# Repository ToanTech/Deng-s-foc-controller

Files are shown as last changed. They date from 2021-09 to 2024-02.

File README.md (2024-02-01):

# 灯哥开源FOC双路无刷电机控制器

      灯哥开源 FOC 控制器是一个由灯哥开源的，基于 [GPL-3.0](https://github.com/ToanTech/Deng-s-foc-controller/blob/master/LICENSE) 开源协议和ESP32主控的低成本无刷电机双路FOC驱动控制板。双路总功率 240W，单路最大功率 120W，支持绝大部分的云台电机FOC 位置、速度、力矩开闭环控制。编码器方面支持常见IIC和ABI、PWM制式。**加入在线电流检测模块，实现真正完整的FOC控制**。总的来说， 灯哥开源 FOC 控制器是一个好用又便宜的双路无刷FOC驱动器，点击查看 [效果视频](https://www.bilibili.com/video/BV1Hz4y127FL/)。

     灯哥开源无刷FOC目前的发展受到灯哥开源团队的深度支持，目前已经针对这块控制板开发出了[灯哥开源无刷四足机器人](https://github.com/ToanTech/py-apple-bldc-quadruped-robot)，DIY视频和效果见：[B站](https://www.bilibili.com/video/BV1kV411i76z/)，后续还有无刷平衡车，倒立摆等等运行示例推出，敬请关注。

* **目前该主控板已经上架淘宝，是焊接好调试好的成品，出售即包括 ESP32** ；有需要大家可以猛击[淘宝链接（进店后在 所有宝贝 处可找到）](https://shop564514875.taobao.com/)

* 开源工作不易，希望大家多点 Star ,视频多一键三联！！！

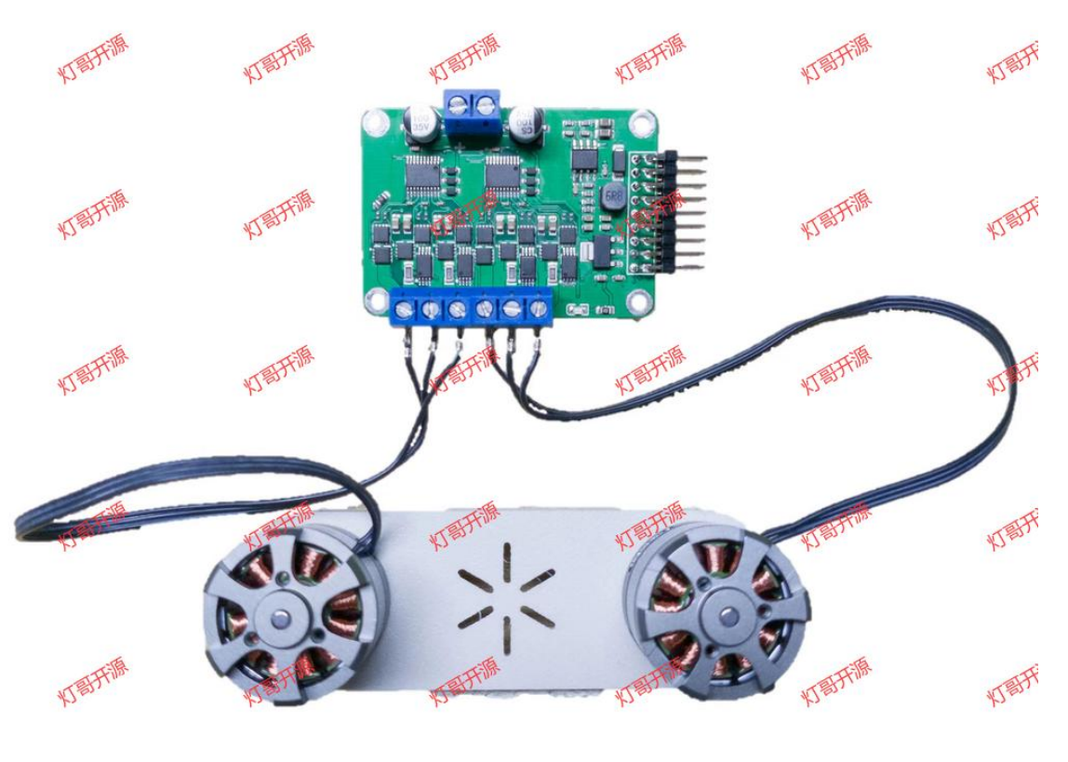
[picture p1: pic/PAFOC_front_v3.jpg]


## 1 软件特性（支持 SimpleFOC库 2.2.2--最新库）

  作为国内最早引入 SimpleFOC 的团队，我们一直在致力深度改进 SimpleFOC硬件使其本土化，让大家能够以低廉的价格玩动无刷FOC算法。SimpleFOC是一个支持强大的开源库，可以实现无刷电机开闭环力矩、速度、位置控制，具体特性如下：

- **基于 Arduino**：运行在 ESP32 Arduino 上

- **开源**: 所有代码和配置文档都可以在：[SimpleFOC文档页](https://docs.simplefoc.com/) 找到

- **轻量化**：相比 Odrive 等驱动器，更加轻量化的软件结构可以帮你高速完成算法学习及配置

- **控制模式丰富**：开/闭环 速度、位置；以及开环的基于力矩控制；两种FOC内核算法

- **图形化配置软件**:最新的 DengFOC 对应支持使用 **SimpleFOC Studio** 进行电机参数配置，如下图所示，配置方法请见 文档PDF

  

## 2 硬件特性

| 说明 | 参数 |
| --- | --- |
| 尺寸 | 56*39 mm |
| 输入电压类型 | 直流DC |
| 输入电压 | 12-24V |
| 最大功率 | 单路120W 双路共240W |
| 支持电机数 | 2 |
| 主控 | 底面搭载ESP32开发板 lolin32 lite |
| 编码器支持 | IIC方式、ABI方式、PWM方式编码器(AS5600、AS5047、AS5048等)、SPI方式、HALL编码器 |
| 拓展接口 | 串口（可以通过串口对FOC板子进行控制） |
| 电流检测参考电压 | 3.3V |
| 电流检测最大电流 | 3.3A |

## 3 重要链接

本 FOC 库与 DengFOC 硬件联合组成一整套完整可用的 FOC 电机驱动方案，资料链接：

1 [灯哥开源 淘宝店--一站配齐DengFOC板](https://shop564514875.taobao.com/) 您的支持就是我们持续做开源内容和课程的动力，项目收益将用于后续开发DengFOC和做课程~

2 [DengFOC库 Github](https://github.com/ToanTech/DengFOC_Lib)

3 [DengFOC官网](http://dengfoc.com/#/) 包含课程文字版讲义，DengFOC使用文档，库使用方法等。

## 4 社区

本FOC板子社区唯三Q群，欢迎加入：**开源FOC无刷驱动交流群 灯哥开源 群号 778255240（1群） 735755513（2群）471832283（3群） 834835665（4群）247431752(5群)**

任何使用问题和 DIY 问题 都会在这里做直接的讨论解答

## 5 项目文件说明

* Dengs FOC V3.0 DIY资料：BOM、原理图、PCB、Gerber
* Dengs FOC V3.0 测试例程：21个灯哥开源FOC开环、闭环、应用方面的测试视频
* 灯哥开源 FOC 使用文档 PDF：**配置的详细方式和使用教程**

## 6 DengFOC配套应用实践项目

利用DengFOC做的有趣的无刷电机实践项目：

[1 动量轮倒立摆项目，低成本化和小型化后应用在DengFOC上](https://github.com/ToanTech/Inverted_Pendulum_DengFOC)

[2 自平衡 DengFOC莱洛三角形](https://github.com/ToanTech/Lailuo_DengFOC)

[3 自平衡 DengFOC无刷平衡车](https://github.com/ToanTech/Balance_Bot_DengFOC)

[4 基于DengFOC的无刷四足并联腿机器狗](https://github.com/ToanTech/py-apple-bldc-quadruped-robot)

## 7 免费手把手教写FOC算法原理课

为了方便大家更进一步的理解FOC的算法和原理，我做了手把手教些FOC算法原理课，通过这些原理课你能够快速的从原理角度理解FOC知识并尝试写出自己的FOC基本功能库，视频链接：

1 [【手把手教写FOC算法】1_起源，无刷电机概念与控制原理](https://www.bilibili.com/video/BV1dy4y1X7yx)

2 [【手把手教写FOC算法】2_克拉克变换，建立简化电机数学模型](https://www.bilibili.com/video/BV1x84y1V76u/)

3 [【手把手教写FOC算法】3_等幅值变换与克拉克逆变换](https://www.bilibili.com/video/BV13s4y1Z7Tg/)

4 [【手把手教写FOC算法】4_帕克变换](https://www.bilibili.com/video/BV1t24y1u7do/)

5a [【手把手教写FOC算法】5a_撰写开环速度代码的前置知识](https://www.bilibili.com/video/BV1Pc411s7mP/)

5b [【手把手教写FOC算法】5b_开环速度代码编程+硬件调试教学](https://www.bilibili.com/video/BV16X4y167XZ/)

6a [【手把手教写FOC算法】6a_撰写闭环位置代码的前置知识](https://www.bilibili.com/video/BV1Rm4y1871K/)

6b [【手把手教写FOC算法】6b_闭环位置代码编程+硬件调试教学](https://www.bilibili.com/video/BV1yh4y1J7Xx/)

7a1 [【手把手教写FOC算法】7a1_写闭环速度代码的前置知识](https://www.bilibili.com/video/BV18m4y1v75j/?spm_id_from=333.788&vd_source=365d5478018f3e4c39b71b3dd6a7dd0a)

7a2[【手把手教写FOC算法】7a2_速度低通滤波器](https://www.bilibili.com/video/BV16h4y1X7gZ/?spm_id_from=333.999.0.0)

7a3 [【手把手教写FOC算法】7a3_速度PI控制器](https://www.bilibili.com/video/BV17s4y1y767/?spm_id_from=333.999.0.0)

7b [【手把手教写FOC算法】7b_闭环速度代码编程+硬件调试教学](https://www.bilibili.com/video/BV1tu4y1o7WU/?spm_id_from=333.999.0.0)

8a [【手把手教写FOC算法】8a_撰写电流环代码的前置知识](https://www.bilibili.com/video/BV1z14y1v7yS/?spm_id_from=333.999.0.0)

8b [【手把手教写FOC算法】8b_精确电流力矩环代码编程+硬件调试教学](https://www.bilibili.com/video/BV1Sh4y1Q7ue/?spm_id_from=333.999.0.0)

9a[【手把手教写FOC算法】9a_用电流环改进速度和位置闭环-前置知识](https://www.bilibili.com/video/BV1Zy4y1A7pL/)

9b[【手把手教写FOC算法】9b_电流环改进速度和位置闭环代码编程+硬件调试教学](https://www.bilibili.com/video/BV1dy4y1N798/)

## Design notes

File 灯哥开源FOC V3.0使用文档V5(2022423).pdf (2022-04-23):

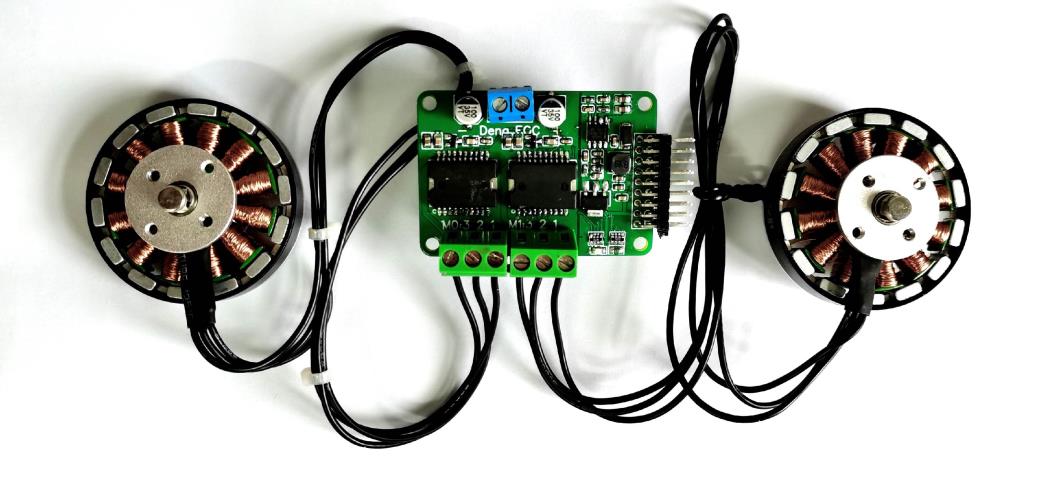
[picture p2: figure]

# 灯哥开源 FOC V3.0

使用说明文档 V5

2022.4.23 更新

1

目录

6 从 0 开始焊接电路板（针对自行 DIY 此 FOC 驱动的爱好者） .....15

2

## 1 概述

灯哥开源 FOC 控制器是一个由灯哥开源的，基于 GPL-3.0 开源

协议和 ESP32 主控的低成本无刷电机双路 FOC 驱动控制板。双路总功

率 240W，单路最大功率 120W，支持绝大部分的云台电机 FOC 位

置、速度、力矩开闭环控制。编码器方面支持常见 IIC 和 ABI、PWM、

Hall、SPI 制式。加入在线电流检测模块，实现真正完整的 FOC 控制。

总的来说，灯哥开源 FOC 控制器是一个好用又便宜的双路无刷 FOC

驱动器。

在 V3 版本中，加入电流检测放大器 INA240A2，通过采样与电机

相串联的采样电阻电压获得 A、B 相电流，应用于电流环控制，构建

出真正，完整的 FOC 算法。

灯哥开源无刷 FOC 目前的发展受到灯哥开源团队的深度支持，目

前已经针对这块控制板开发出了灯哥开源无刷四足机器人，后面更会

开发出更多好玩的应用，例如平衡车，倒立摆等等，敬请关注。

## 2 性能简介

### 2.1 总体性能

目前灯哥开源双路 FOC 的具体技术性能指标如下：

单路最大功率 | 120W（双路 240W）
支持电压 | 12V-24V
支持的无刷电机类型 | 云台电机（相电阻>10 欧）

3

支持同时驱动的电机数量 | 2
支持的编码器通讯方式 | IIC ABI PWM Hall SPI
支持的外部控制方式 | 串口控制 WIFI 无线控制
支持的电流检测方式 | 在线电流检测
电流检测电压 | 3.3V
电流检测最大电流 | 3.3A

### 2.2 驱动板支持的电机选型

灯哥开源 FOC 目前支持常见的云台电机，具体选型指标主要有两

点：

◼ 电机相电阻>10Ω

◼ 最大运行电流在 5A 左右

这两个选型指标基本上能够覆盖大部分的云台电机，所以基本上只

要选择云台电机就可以正常的使用这个板子，若按照 KV 数进行选择，

建议选择 200KV 以下的电机。

若对云台电机的选型有疑问，或者需要验证选型是否正确，可以加

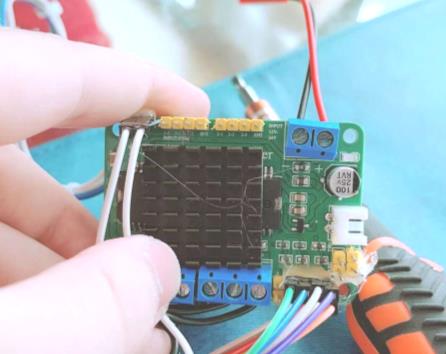
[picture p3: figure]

4

入 Q 群：778255240 详细询问，热心的群友将会给你解答，灯哥我看

到了也会及时回复。

## 3 基础配置及运行

### 3.1 线路连接及其实例

灯哥开源 FOC V3 的线路连接与 V2 相同，极其简单，只需要连上电

源线和电机线，就已经可以使得板子正常的运行开环控制；在此基础

上，再连接上编码器，就可以使 FOC 控制板实现闭环控制。

注意：若需要长时间调试或使用，你得加上散热片，良好的散热能

够使得 FOC 的性能得到充分发挥！实验证明，大部分运行过程中突

然的卡顿。震动都来自于 FOC 散热不良！！在高电压电流的情况下，

不良的 FOC 散热有可能导致驱动芯片烧毁。在默认情形下，灯哥官

方建议一般都必须加上散热片使用！

推荐的散热片尺寸为 25x25 铝制散热片，安装效果如下图所示：

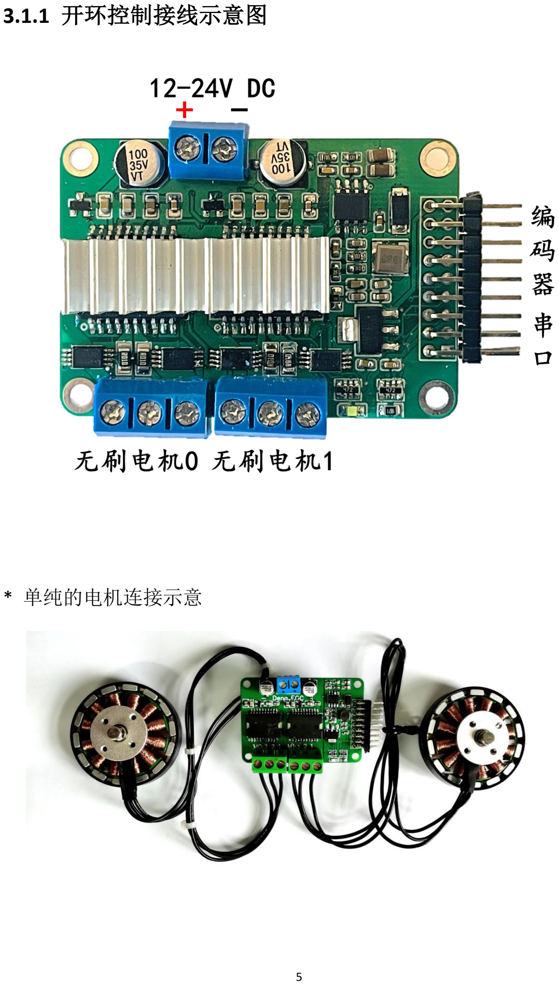
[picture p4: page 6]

5

### 3.1.1 开环控制接线示意图

* 单纯的电机连接示意

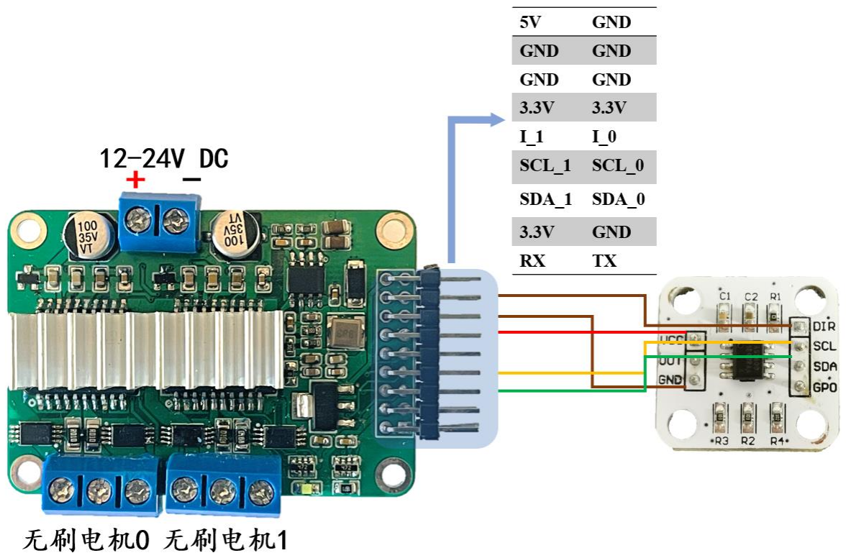
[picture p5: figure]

6

### 3.1.2 闭环控制接线图（基于 AS5600）

由于图幅限制，只展示一个电机配合一个编码器的接线，两个电

机的接线亦同理，具体例程请参照例程文件夹。

### 3.1.3 闭环控制接线图（基于 AS5047P）

由于图幅限制，只展示一个电机配合一个编码器的接线，两个电

机的接线亦同理，具体例程请参照例程文件夹。

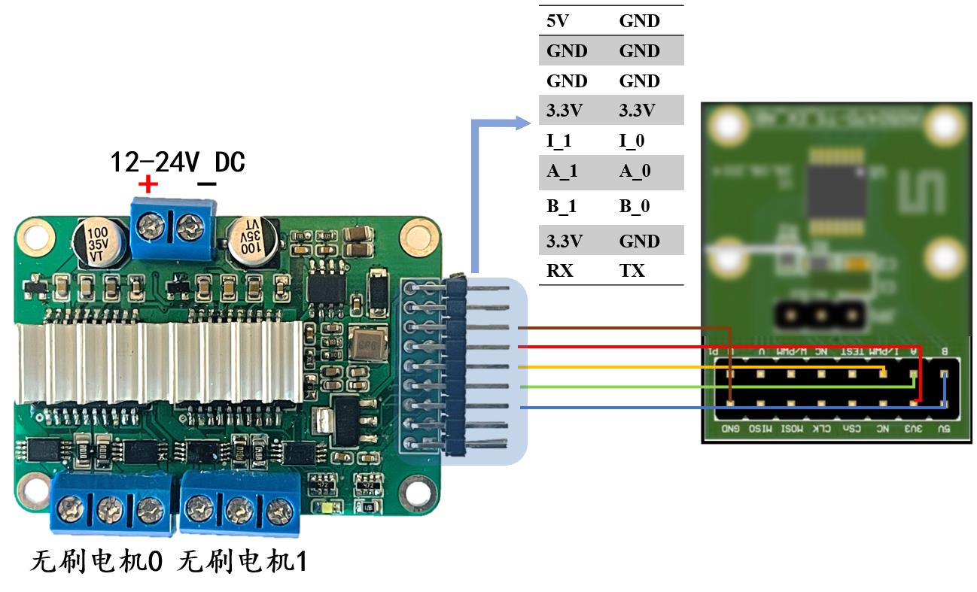
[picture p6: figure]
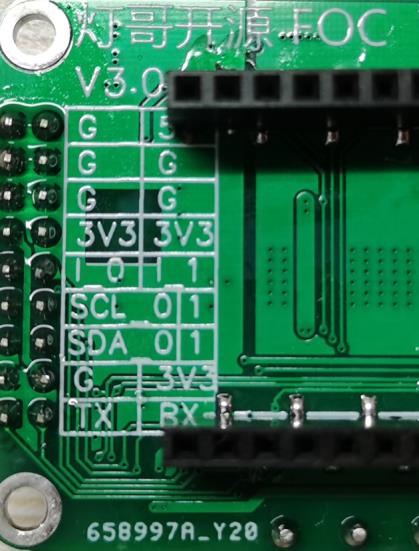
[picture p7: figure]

7

* 底面均有引脚示意

在完成了对应的接线，通电确定驱动板灯亮之后，就可以进入我

们的下一步：编程环境配置

### 3.2 编程环境配置

灯哥开源 FOC 由于使用基于 SimpleFOC 的库运行，因此软件环境配

8

置也与 SimpleFOC 库相同，默认都采用 Arduino IDE 作为主程序编程

/编译软件。

最新测试过能够完美支持灯哥开源 FOC 的软件版本为：

✓ Arduino IDE 1.8.19

✓ SimpleFOC Library 2.2.1

✓ ESP32 Arduino Libiary 2.0.2

针对上面的软件版本，我已经做好整合包，大家直接下载解压就可

以使用，避免繁杂的环境配置，下载地址：

⚫ 链接：

https://pan.baidu.com/s/13VfSVINak0wqCzG9hRQUYA?pwd=wumh

⚫ 提取码：wumh

当完成下载后，解压下载的文件，点击文件中的 arduino.exe 即可

打开软件，开始编译例程，愉快的玩耍。

注意：解压前建议清除原有 Arduino 的环境；解压路径不要有中文路

径。

完成安装后，即可编译本项目提供的例程。并且进行程序的编写。

在下幅图中，点击左上角的“√”进行程序的编译，当电脑连接了

FOC 控制板后，点击左上角的“→”进行程序上传，接下来就可以畅

快的玩耍了。

注意，开发板必须选择：ESP32 DEV Module,具体选择方式如下,

必须如图上设置好之后才能编译并且使用：

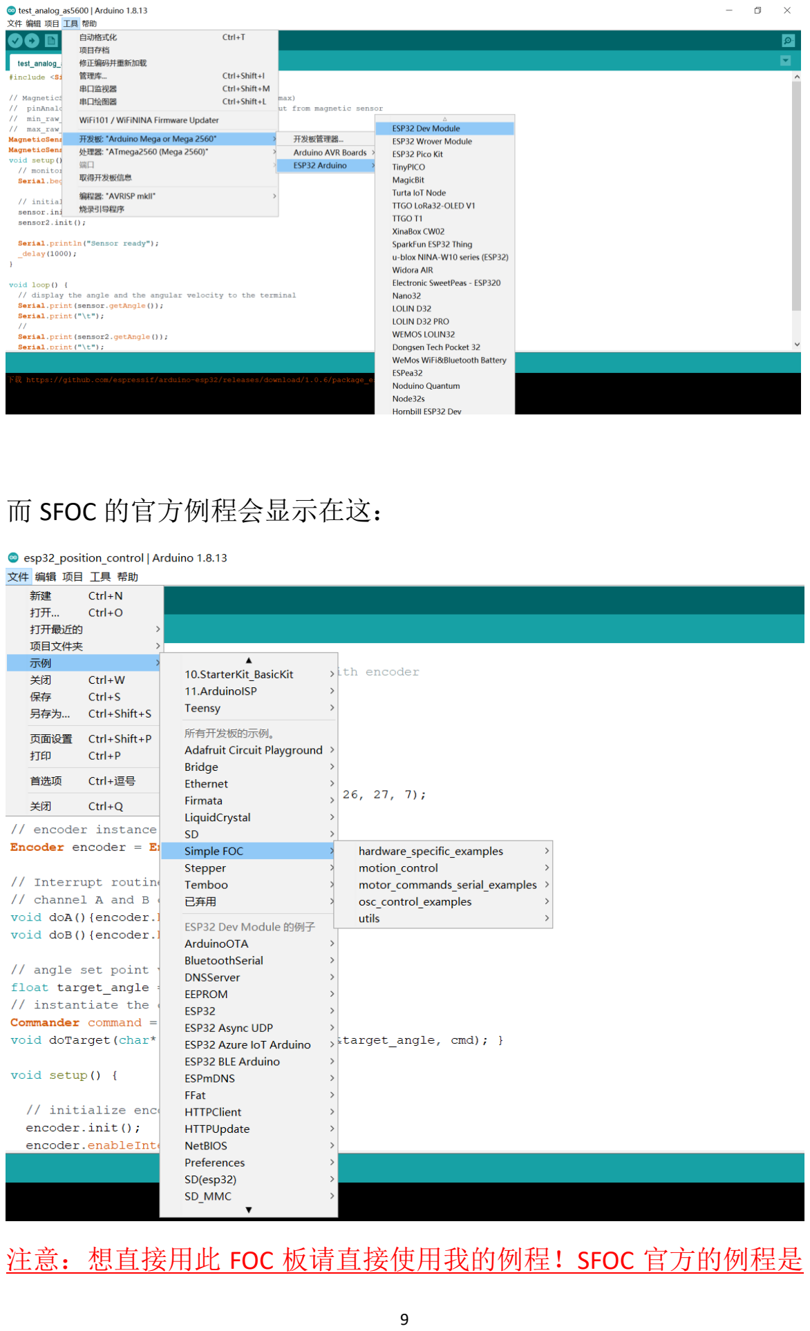
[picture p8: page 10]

9

而 SFOC 的官方例程会显示在这：

注意：想直接用此 FOC 板请直接使用我的例程！SFOC 官方的例程是

10

针对官方板子的，引脚不一样！不修改不能直接用在此板子上！而我

给大家的例程都是已经改好调试过的！！

## 4 Simple FOC Studio 在线调参工具

4.1 简介

SimpleFOC Studio 是一个可用于图形化配置 SimpleFOC，并且对电

机进行在线 PID 调参的工具，非常好用，主要特性包括：

1. 电机参数的实时调整和配置
2. 电机状态的实时绘图和监控
3. 可以根据配置好的参数自动生成代码，以植入到自己的程序中
4. 基于 PyQT5 安装配置简单，兼容性好。

软件的操作界面如下图所示，在本章中，将会详细讲述它的配置方式。

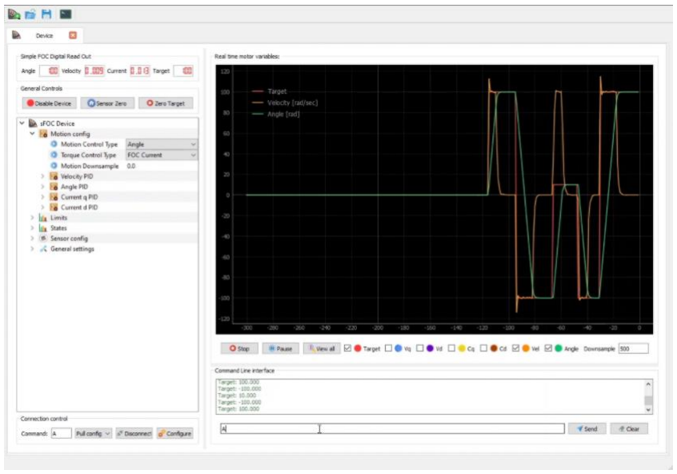
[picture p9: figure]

11

### 4.2 安装及配置

### 4.2.1 方法 1

SimpleFOCStudio 的安装非常简易，就算你没有使用过终端的， 也只

需以下几步:

1. 如果你还没有安装 Python,安装 Python

⚫ 我们建议用 Anaconda，这样安装起来会更方便 点击查看如何安装 (https://docs.anaconda.com/anaconda/install/)

⚫ 当你的 Anaconda 开始成功运行时，打开 CMD 命令提示符，输入：

conda create -n simplefoc python=3.6.0

⚫ 运行完这一句后，再运行下面的这条指令:

conda activate simplefoc

2. 进入 SimpleFOCStudio (https://github.com/JorgeMaker/SimpleFOCStudio) 页面，克隆仓库或者再首页下载 zip 文件，

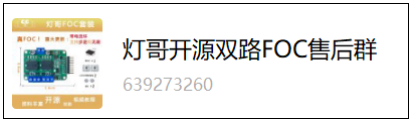
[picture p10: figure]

12

解压

3. 用 CMD 进入解压后的文件夹，命令应该长得像下面这样

cd some_path_on_disk/SimpleFOCStudio

4. 最后一步是安装 SimpleFOCStudio 的必须库，用如下命令:

pip install -r "requirements.txt"

当你完成了安装后，需要启动软件，只需要再 SimpleFOCStudio 文

件夹中运行代码如下:

python simpleFOCStudio.py

或者在 Anaconda 中输入:

conda activate simplefoc

python simpleFOCStudio.py

即可启动软件，更多用法请见：SimpleFOCStudio (https://github.com/JorgeMaker/SimpleFOCStudio)

### 4.2.2 方法 2

如果你是在淘宝店购买板子的客户，可以进入到我们的售后群中：

在“群文件”中，可以找到已经编译为 EXE，可直接使用的版本，如

下图红色框框住的文件所示，直接解压后即可使用：

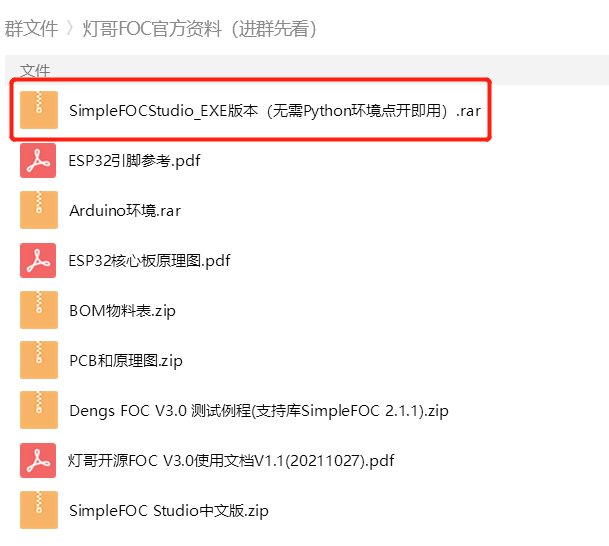
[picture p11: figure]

13

## 5 例程及其注释

注释详见例程文件夹中的程序,实例程序列表如下：

灯哥开源 FOC 海量例程代码合集

1 双电机开环速度控制

2 双电机开环位置控制

3 IIC 双编码器测试(AS5600)

4 ABI 双编码器测试(AS5047P)

5 双电机闭环速度控制

6 双电机闭环位置控制

7 双电机闭环位置力矩互控

8 灯哥开源机器狗专用程序（通过串口控制此 FOC 驱动板）

14

9 双电机电流环 FOC 力矩控制

10 一个电机作为旋钮，另外一个电机输出速度

11 SimpleFOC Studio 快速调节 PID-驱动板端例程—M0 端

12 SimpleFOC Studio 快速调节 PID-驱动板端例程—M1 端

13 双电机在线电流检测测试

14 步进电机开环速度测试

15 SPI 编码器测试(AS5047P)

16 步进电机闭环速度测试(AS5600)

17 步进电机闭环位置测试(AS5600)

18 步进电机闭环速度测试(AS5047P)

19 步进电机闭环位置测试(AS5047P)

20 步进电机 StepDir 信号接收测试

21 步进电机改无刷例程（StepDir 信号控制无刷电机测试）

22 霍尔编码器测试(5 线)

23 双霍尔电机闭环测试(5 线)

24 应用实例项目-动量轮自平衡倒立摆

25 应用实例项目-灯哥无刷四足机器人

例程运行标准效果视频：

效果运行视频 (https://www.bilibili.com/video/BV1QU4y1p7Z6/)

测试自己板子时可以根据此视频查看自己的板子是否达到标准效果。

15

## 6 从0开始焊接电路板（针对自行DIY此FOC

## 驱动的爱好者）

手把手焊接教学 (https://www.bilibili.com/video/BV1QU4y1p7Z6?p=2)

## 7 常见问题及其解决

### 7.1 电机不转

1. 检查电机的接线是否正常
2. 检查电源是否没电
3. 检查程序是否正确
4. 检查电机内部是否断线

### 7.2 电机抖动

1. 检查电机接线，是否存在缺相
2. 检查程序中的极对数设置是否正确（一般震动现象大部分来源于

极对数设置错误）

3. 测试开环速度例程，如果由于速度设置过高引起震动，可以把速

度设置低些

### 7.3 电机或芯片剧烈发热

1. 电机不要运动在震动状态下

16

2. 开环速度例程，速度不要长期设置为 0（否则类似堵转，会发热），

若要取得实用效果，建议闭环

3. 开环位置例程，位置不要长期不变（否则类似堵转，会发热），

若要取得实用效果，建议闭环

### 7.4 编码器读数跳变

1. 检查编码器磁铁安装是否正确（轴向，径向磁铁要分清）
2. AS5600 的话，检查是否 dir 接入高电平或者低电平（GND）
3. 检查磁铁和编码器得距离是否过远

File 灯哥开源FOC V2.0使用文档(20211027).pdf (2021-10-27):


# 灯哥开源 FOC V2.0

使用说明文档 V2.1

2021.10.27 更新

1

目录

6 从 0 开始焊接电路板（针对自行 DIY 此 FOC 驱动的爱好者） .....12

2

## 1 概述

灯哥开源 FOC 控制器是一个由灯哥开源的，基于 Apache 2.0 开

源协议和 ESP32 主控芯片的低成本无刷电机双路 FOC 驱动控制板。双

路总功率 240W，单路最大功率 120W，支持绝大部分的云台电机。

编码器方面，支持常见 IIC、PWM 以及 ABI 制式编码器。是一个好用

又便宜的双路无刷 FOC 驱动器。

灯哥开源无刷 FOC 目前的发展受到灯哥开源团队的深度支持，目

前已经针对这块控制板开发出了灯哥开源无刷四足机器人，后面更会

开发出更多好玩的应用，例如平衡车，倒立摆等等，敬请关注。

## 2 性能简介

### 2.1 总体性能

目前灯哥开源双路 FOC 的具体技术性能指标如下：

单路最大功率 | 120W（双路 240W）
支持电压 | 12V-24V
支持的无刷电机类型 | 云台电机（相电阻>10 欧）
支持同时驱动的电机数量 | 2
支持的编码器通讯方式 | IIC 模拟方式 ABI PWM

3

支持的外部控制方式 | 串口控制
| WIFI 无线控制

### 2.2 驱动板支持的电机选型

灯哥开源 FOC 目前支持常见的云台电机，具体选型指标主要有两

点：

◼ 电机相电阻>10Ω

◼ 最大运行电流在 5A 左右

这两个选型指标基本上能够覆盖大部分的云台电机，所以基本上只

要选择云台电机就可以正常的使用这个板子，若按照 KV 数进行选择，

建议选择 200KV 以下的电机。

若对云台电机的选型有疑问，或者需要验证选型是否正确，可以加

入 Q 群：778255240 详细询问，热心的群友将会给你解答，灯哥我看

到了也会及时回复。

## 3 基础配置及运行

### 3.1 线路连接及其实例

灯哥开源 FOC 的线路连接极其简单，只需要连上电源线和电机线，

就已经可以使得板子正常的运行开环控制；在此基础上，再连接上编

码器，就可以使 FOC 控制板实现闭环控制。

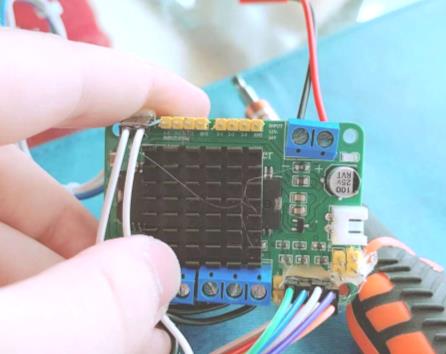
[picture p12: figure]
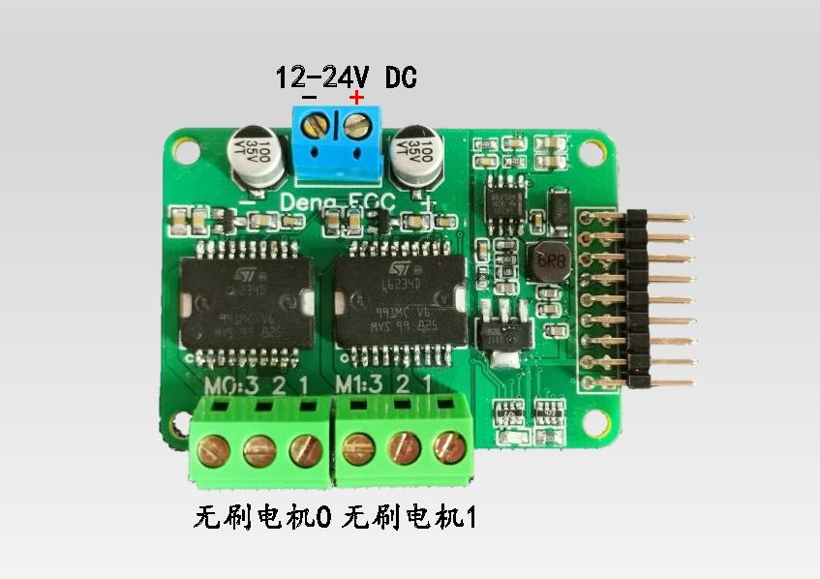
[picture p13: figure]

4

注意：若需要长时间调试或使用，你得加上散热片，良好的散热能

够使得 FOC 的性能得到充分发挥！实验证明，大部分运行过程中突

然的卡顿。震动都来自于 FOC 散热不良！！在高电压电流的情况下，

不良的 FOC 散热有可能导致驱动芯片烧毁。在默认情形下，灯哥官

方建议一般都必须加上散热片使用！

推荐的散热片尺寸为 25x25 铝制散热片，安装效果如下图所示：

### 3.1.1 开环控制接线示意图

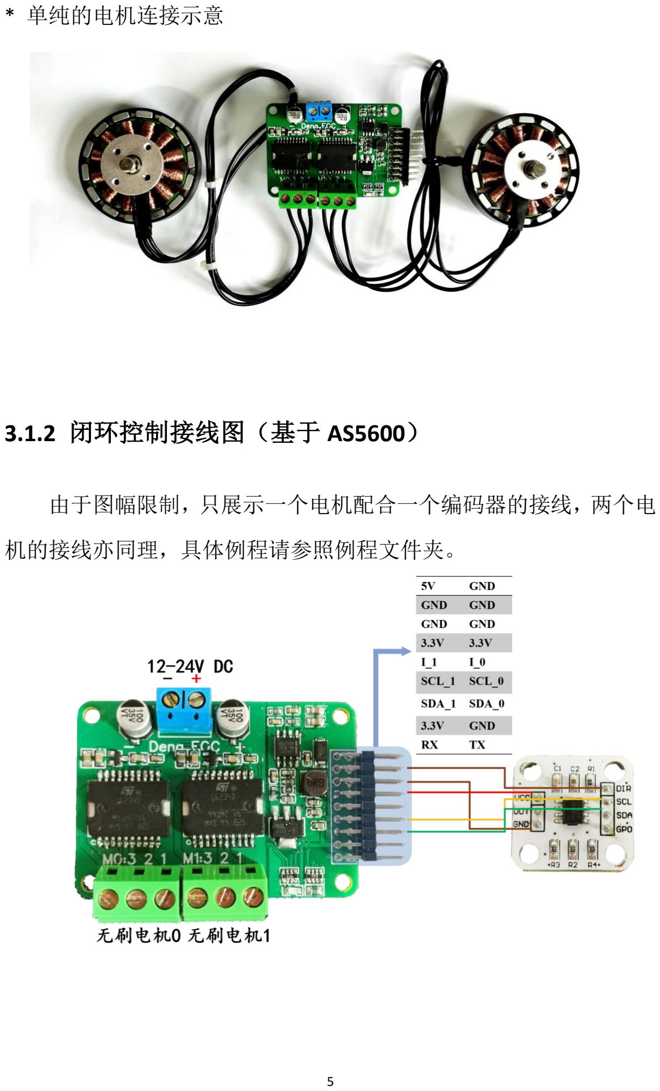
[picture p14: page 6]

5

* 单纯的电机连接示意

### 3.1.2 闭环控制接线图（基于 AS5600）

由于图幅限制，只展示一个电机配合一个编码器的接线，两个电

机的接线亦同理，具体例程请参照例程文件夹。

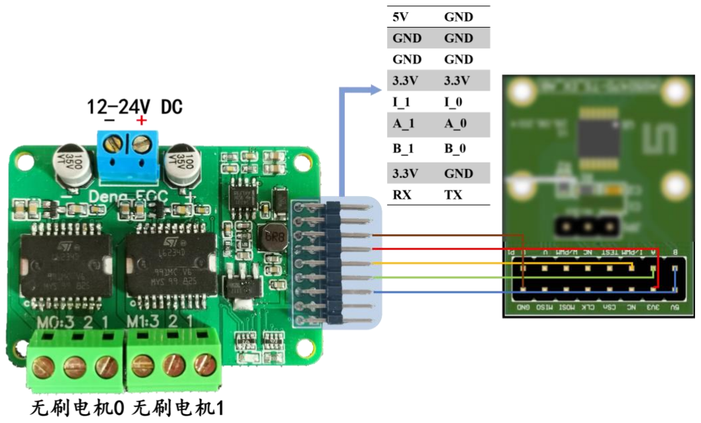
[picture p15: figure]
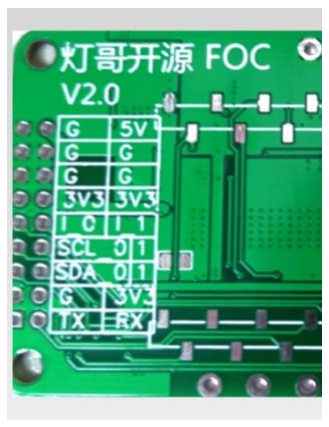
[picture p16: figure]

6

### 3.1.3 闭环控制接线图（基于 AS5047P）

由于图幅限制，只展示一个电机配合一个编码器的接线，两个电

机的接线亦同理，具体例程请参照例程文件夹。

* 底面均有引脚示意

在完成了对应的接线，通电确定驱动板灯亮之后，就可以进入我

们的下一步：编程环境配置

7

### 3.2 编程环境配置

灯哥开源 FOC 由于使用基于 SimpleFOC 的库运行，因此软件环境配

置也与 SimpleFOC 库相同，默认都采用 Arduino IDE 作为主程序编程

/编译软件。

最新测试过能够完美支持灯哥开源 FOC 的软件版本为：

✓ Arduino IDE 1.8.13

✓ SimpleFOC Library 2.1.1

✓ ESP32 Arduino Libiary 1.0.4

针对上面的软件版本，我已经做好整合包，大家直接下载解压就可

以使用，避免繁杂的环境配置，下载地址：

◼ Github：Github (https://github.com/ToanTech/Deng-s-foc-controller) 下载地址 (https://github.com/ToanTech/Deng-s-foc-controller)

◼ Gitee（国内访问速度最快）：Gitee (https://gitee.com/ream_d/Deng-s-foc-controller) 下载地址 (https://gitee.com/ream_d/Deng-s-foc-controller)

当完成下载后，解压下载的文件，点击文件中的 arduino.exe 即可

打开软件，开始编译例程，愉快的玩耍。

完成安装后，即可编译本项目提供的例程。并且进行程序的编写。

在下幅图中，点击左上角的“钩”进行程序的编译，当电脑连接了

FOC 控制板后，点击左上角的“小箭头”进行程序上传，接下来就可

以畅快的玩耍了。

注意，开发板必须选择：ESP32 DEV Module,具体选择方式如下,

必须如图上设置好之后才能编译并且使用：

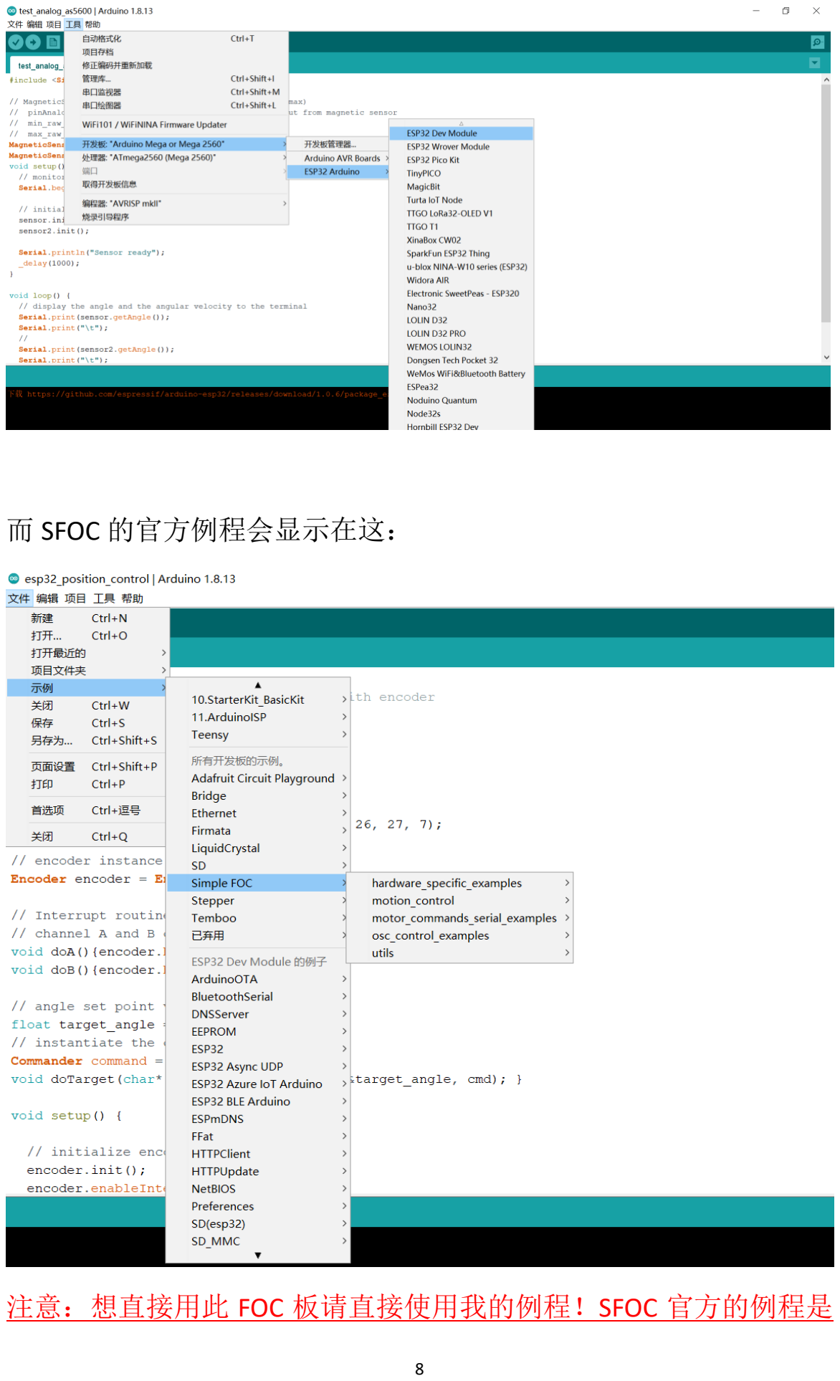
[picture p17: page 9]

8

而 SFOC 的官方例程会显示在这：

注意：想直接用此 FOC 板请直接使用我的例程！SFOC 官方的例程是

9

针对官方板子的，引脚不一样！不修改不能直接用在此板子上！而我

给大家的例程都是已经改好调试过的！！

## 4 Simple FOC Studio 在线调参工具

4.1 简介

SimpleFOC Studio 是一个可用于图形化配置 SimpleFOC，并且对电

机进行在线 PID 调参的工具，非常好用，主要特性包括：

1. 电机参数的实时调整和配置
2. 电机状态的实时绘图和监控
3. 可以根据配置好的参数自动生成代码，以植入到自己的程序中
4. 基于 PyQT5 安装配置简单，兼容性好。

软件的操作界面如下图所示，在本章中，将会详细讲述它的配置方式。


10

### 4.2 安装及配置

SimpleFOCStudio 的安装非常简易，就算你没有使用过终端的， 也只

需以下几步:

1. 如果你还没有安装 Python,安装 Python

⚫ 我们建议用 Anaconda，这样安装起来会更方便 点击查看如何安装 (https://docs.anaconda.com/anaconda/install/)

⚫ 当你的 Anaconda 开始成功运行时，打开 CMD 命令提示符，输入：

conda create -n simplefoc python=3.6.0

⚫ 运行完这一句后，再运行下面的这条指令:

conda activate simplefoc

2. 进入 SimpleFOCStudio (https://github.com/JorgeMaker/SimpleFOCStudio) 页面，克隆仓库或者再首页下载 zip 文件，

解压

3. 用 CMD 进入解压后的文件夹，命令应该长得像下面这样

11

cd some_path_on_disk/SimpleFOCStudio

4. 最后一步是安装 SimpleFOCStudio 的必须库，用如下命令:

pip install -r "requirements.txt"

当你完成了安装后，需要启动软件，只需要再 SimpleFOCStudio 文

件夹中运行代码如下:

python simpleFOCStudio.py

或者在 Anaconda 中输入:

conda activate simplefoc

python simpleFOCStudio.py

即可启动软件，更多用法请见：SimpleFOCStudio (https://github.com/JorgeMaker/SimpleFOCStudio)

## 5 例程及其注释

注释详见例程文件夹中的程序,实例程序列表如下：

编号 | 例程详情
1 | 双电机开环速度控制
2 | 双电机开环位置控制
3 | IIC 双编码器测试(AS5600)
4 | ABI 双编码器测试(AS5047P)
5 | 双电机闭环速度控制
6 | 一个电机作为旋钮，另外一个电机输出速度
7 | 双电机闭环位置/力矩互控
8 | 灯哥开源机器狗专用程序（通过串口控制此 FOC 驱动板）
9 | 灯哥开源机器狗专用程序（通过串口控制此 FOC 驱动板）

12

10 | 双电机力矩控制
11 | SimpleFOC Studio 快速调节 PID-驱动板端例程

例程运行标准效果视频：

效果运行视频 (https://www.bilibili.com/video/BV1QU4y1p7Z6/)

测试自己板子时可以根据此视频查看自己的板子是否达到标准效果。

## 6 从0开始焊接电路板（针对自行DIY此FOC

## 驱动的爱好者）

手把手焊接教学（当前 (https://www.bilibili.com/video/BV1QU4y1p7Z6?p=2) V2.0 版本的焊接教程仍在准备中，目前连接

直接去的是 V1.0 版本的焊接教程）

## 7 常见问题及其解决

### 7.1 电机不转

1. 检查电机的接线是否正常
2. 检查电源是否没电
3. 检查程序是否正确
4. 检查电机内部是否断线

### 7.2 电机抖动

1. 检查电机接线，是否存在缺相

13

2. 检查程序中的极对数设置是否正确（一般震动现象大部分来源于

极对数设置错误）

3. 测试开环速度例程，如果由于速度设置过高引起震动，可以把速

度设置低些

### 7.3 电机或芯片剧烈发热

1. 电机不要运动在震动状态下
2. 开环速度例程，速度不要长期设置为 0（否则类似堵转，会发热），

若要取得实用效果，建议闭环

3. 开环位置例程，位置不要长期不变（否则类似堵转，会发热），

若要取得实用效果，建议闭环

### 7.4 编码器读数跳变

1. 检查编码器磁铁安装是否正确（轴向，径向磁铁要分清）
2. AS5600 的话，检查是否 dir 接入高电平或者低电平（GND）
3. 检查磁铁和编码器得距离是否过远

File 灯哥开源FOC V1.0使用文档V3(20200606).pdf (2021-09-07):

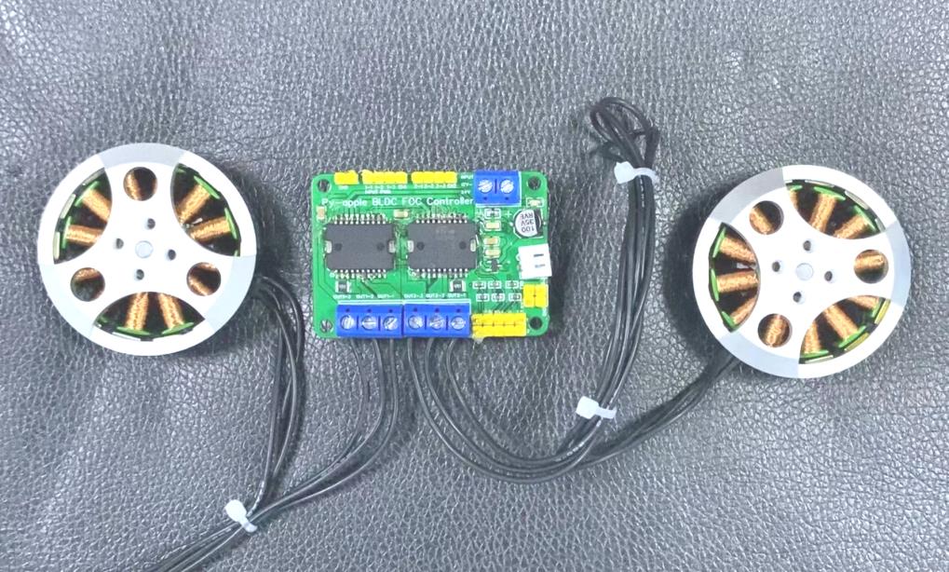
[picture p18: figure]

# 灯哥开源 FOC V1.0

使用说明文档 V3

2020.6.6 更新

1

目录

6 从 0 开始焊接电路板（针对自行 DIY 此 FOC 驱动的爱好者） .....11

2

## 1 概述

灯哥开源 FOC 控制器是一个由灯哥开源的，基于 Apache 2.0 开

源协议和 ESP32 主控芯片的低成本无刷电机双路 FOC 驱动控制板。双

路总功率 240W，单路最大功率 120W，支持绝大部分的云台电机。

编码器方面，支持常见 IIC 和 ABI 制式编码器。是一个好用又便宜的

双路无刷 FOC 驱动器。

灯哥开源无刷 FOC 目前的发展受到灯哥开源团队的深度支持，目

前已经针对这块控制板开发出了灯哥开源无刷四足机器人，后面更会

开发出更多好玩的应用，例如平衡车，倒立摆等等，敬请关注。

## 2 性能简介

### 2.1 总体性能

目前灯哥开源双路 FOC 的具体技术性能指标如下：

单路最大功率 | 120W（双路 240W）
支持电压 | 12V-24V
支持的无刷电机类型 | 云台电机（相电阻>10 欧）
支持同时驱动的电机数量 | 2
支持的编码器通讯方式 | IIC 模拟方式 ABI PWM

3

支持的外部控制方式 | 串口控制
| WIFI 无线控制

### 2.2 驱动板支持的电机选型

灯哥开源 FOC 目前支持常见的云台电机，具体选型指标主要有两

点：

◼ 电机相电阻>10Ω

◼ 最大运行电流在 5A 左右

这两个选型指标基本上能够覆盖大部分的云台电机，所以基本上只

要选择云台电机就可以正常的使用这个板子，若按照 KV 数进行选择，

建议选择 200KV 以下的电机。

若对云台电机的选型有疑问，或者需要验证选型是否正确，可以加

入 Q 群：778255240 详细询问，热心的群友将会给你解答，灯哥我看

到了也会及时回复。

## 3 基础配置及运行

### 3.1 线路连接及其实例

灯哥开源 FOC 的线路连接及其简单，只需要连上电源线和电机线，

就已经可以使得板子正常的运行开环控制；在此基础上，再连接上编

码器，就可以使 FOC 控制板实现闭环控制。


4

注意：若需要长时间调试或使用，你得加上散热片，良好的散热能

够使得 FOC 的性能得到充分发挥！实验证明，大部分运行过程中突

然的卡顿。震动都来自于 FOC 散热不良！！在高电压电流的情况下，

不良的 FOC 散热有可能导致驱动芯片烧毁。在默认情形下，灯哥官

方建议一般都必须加上散热片使用！

推荐的散热片尺寸为 25x25 铝制散热片，安装效果如下图所示：

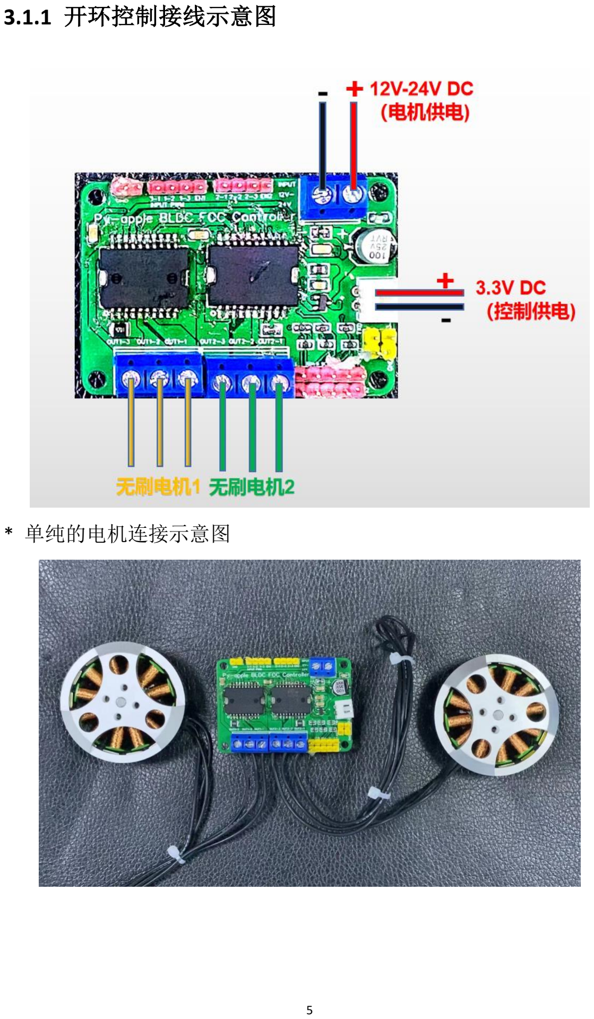
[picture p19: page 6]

5

### 3.1.1 开环控制接线示意图

* 单纯的电机连接示意图

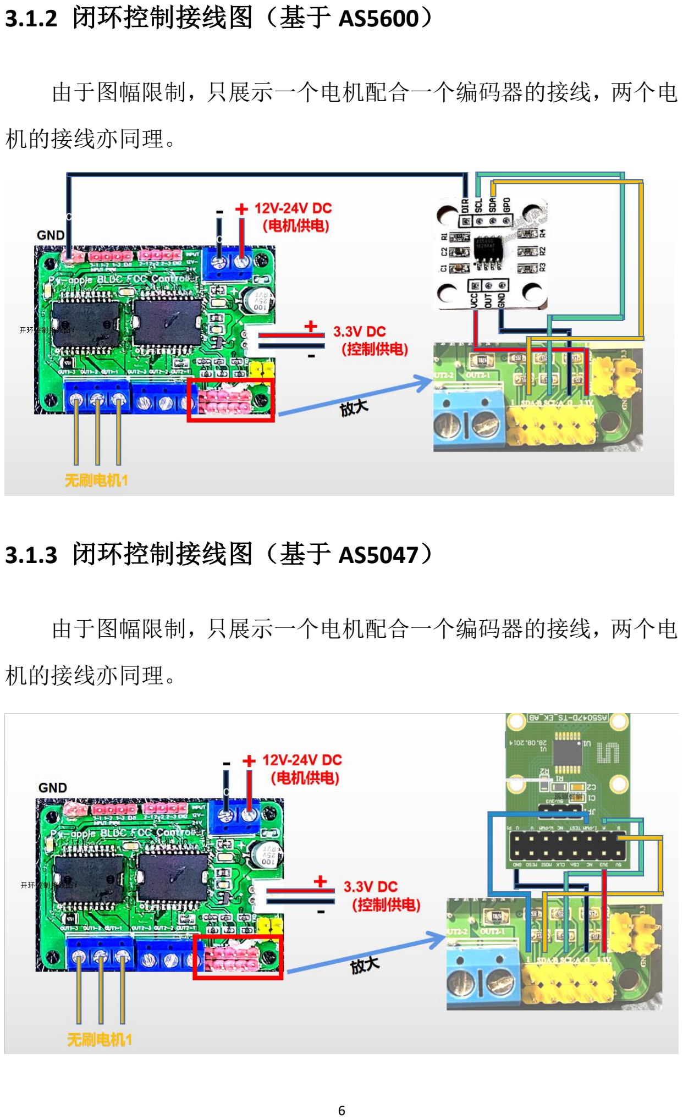
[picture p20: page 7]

6

### 3.1.2 闭环控制接线图（基于 AS5600）

由于图幅限制，只展示一个电机配合一个编码器的接线，两个电

机的接线亦同理。

### 3.1.3 闭环控制接线图（基于 AS5047）

由于图幅限制，只展示一个电机配合一个编码器的接线，两个电

机的接线亦同理。

7

在完成了对应的接线，通电确定驱动板灯亮之后，就可以进入我

们的下一步：编程环境配置

### 3.2 编程环境配置

灯哥开源 FOC 由于使用基于 SimpleFOC 的库运行，因此软件环境配

置也与 SimpleFOC 库相同，默认都采用 Arduino IDE 作为主程序编程

/编译软件。

最新测试过能够完美支持灯哥开源 FOC 的软件版本为：

✓ Arduino IDE 1.8.13

✓ SimpleFOC Library 2.1.1

✓ ESP32 Arduino Libiary 1.0.4

针对上面的软件版本，我已经做好整合包，大家直接下载就可以使

用，避免繁杂的环境配置，下载地址：

◼ Github：Github (https://github.com/ToanTech/Deng-s-foc-controller/tree/main/%E7%81%AF%E5%93%A5%E5%BC%80%E6%BA%90FOC%E4%B8%93%E7%94%A8%20Arduino%20%E7%BC%96%E7%A8%8B%E7%8E%AF%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) 下载地址 (https://github.com/ToanTech/Deng-s-foc-controller/tree/main/%E7%81%AF%E5%93%A5%E5%BC%80%E6%BA%90FOC%E4%B8%93%E7%94%A8%20Arduino%20%E7%BC%96%E7%A8%8B%E7%8E%AF%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)

◼ Gitee（国内访问速度最快）：Gitee (https://gitee.com/ream_d/Deng-s-foc-controller/tree/main/%E7%81%AF%E5%93%A5%E5%BC%80%E6%BA%90FOC%E4%B8%93%E7%94%A8%20Arduino%20%E7%BC%96%E7%A8%8B%E7%8E%AF%E5%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) 下载地址 (https://gitee.com/ream_d/Deng-s-foc-controller/tree/main/%E7%81%AF%E5%93%A5%E5%BC%80%E6%BA%90FOC%E4%B8%93%E7%94%A8%20Arduino%20%E7%BC%96%E7%A8%8B%E7%8E%AF%E5%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)

当完成下载后，解压下载的文件，其中：

✓ "to Program Files" 文件夹中的内容复制到 C:\Program Files (x86)

✓ "to Documents" 文件夹中的内容复制到 C:\Users\你的电脑用户

名\Documents\Arduino

✓ "to Local"文件夹中的内容复制到 C:\Users\你的电脑用户名

\AppData\Local

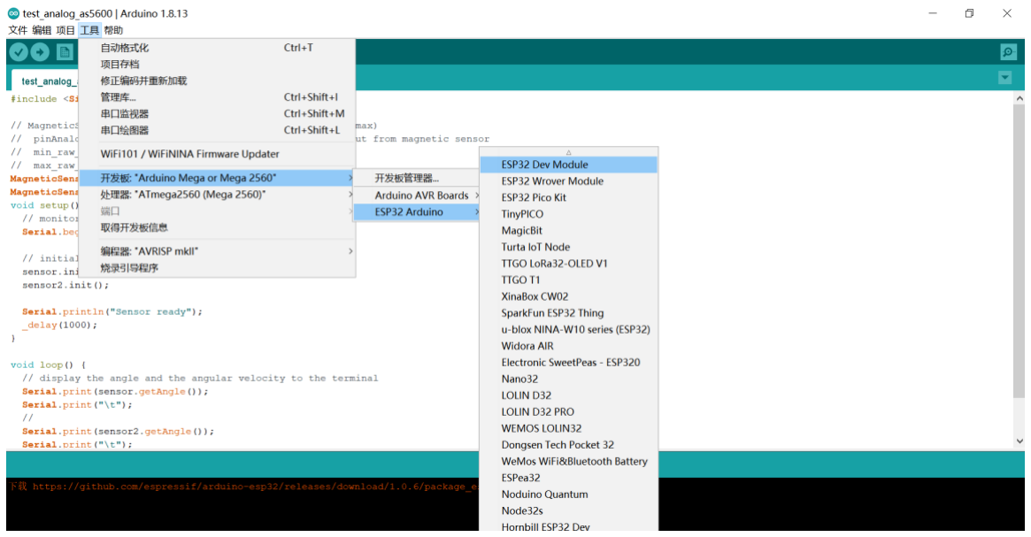
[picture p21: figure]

8

完 成 这 三 步 后 ， 点 击 C:\Program Files (x86)\Arduino 中的

arduino.exe 即可打开软件，开始编译例程，愉快的玩耍

完成安装后，即可编译本项目提供的例程。并且进行程序的编写。

在下幅图中，点击左上角的“钩”进行程序的编译，当电脑连接了

FOC 控制板后，点击左上角的“小箭头”进行程序上传，接下来就可

以畅快的玩耍了。

注意，开发板必须选择：ESP32 DEV Module,具体选择方式如下,

必须如图上设置好之后才能编译并且使用：

## 4 Simple FOC Studio 在线调参工具

4.1 简介

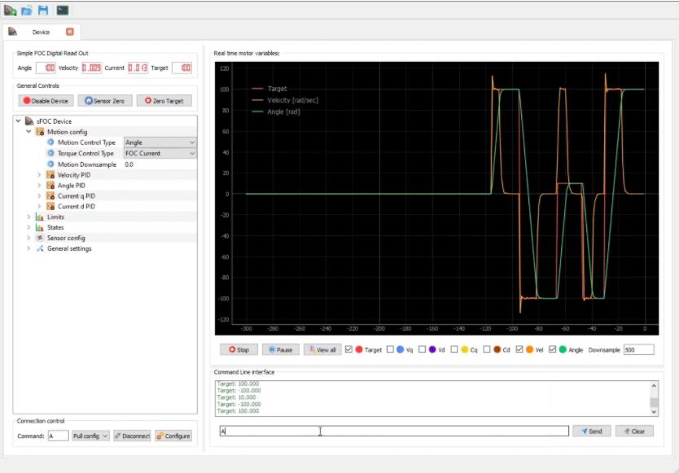
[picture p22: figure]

9

SimpleFOC Studio 是一个可用于图形化配置 SimpleFOC，并且对电

机进行在线 PID 调参的工具，非常好用，主要特性包括：

1. 电机参数的实时调整和配置
2. 电机状态的实时绘图和监控
3. 可以根据配置好的参数自动生成代码，以植入到自己的程序中
4. 基于 PyQT5 安装配置简单，兼容性好。

软件的操作界面如下图所示，在本章中，将会详细讲述它的配置方式。

### 4.2 安装及配置

SimpleFOCStudio 的安装非常简易，就算你没有使用过终端的， 也只

需以下几步:

1. 如果你还没有安装 Python,安装 Python

10

⚫ 我们建议用 Anaconda，这样安装起来会更方便 点击查看如何安装 (https://docs.anaconda.com/anaconda/install/)

⚫ 当你的 Anaconda 开始成功运行时，打开 CMD 命令提示符，输入：

conda create -n simplefoc python=3.6.0

⚫ 运行完这一句后，再运行下面的这条指令:

conda activate simplefoc

2. 进入 SimpleFOCStudio (https://github.com/JorgeMaker/SimpleFOCStudio) 页面，克隆仓库或者再首页下载 zip 文件，

解压

3. 用 CMD 进入解压后的文件夹，命令应该长得像下面这样

cd some_path_on_disk/SimpleFOCStudio

4. 最后一步是安装 SimpleFOCStudio 的必须库，用如下命令:

pip install -r "requirements.txt"

当你完成了安装后，需要启动软件，只需要再 SimpleFOCStudio 文

件夹中运行代码如下:

python simpleFOCStudio.py

或者在 Anaconda 中输入:

conda activate simplefoc

python simpleFOCStudio.py

即可启动软件，更多用法请见：SimpleFOCStudio (https://github.com/JorgeMaker/SimpleFOCStudio)

## 5 例程及其注释

注释详见例程文件夹中的程序,实例程序列表如下：

编号 | 例程详情
1 | 双电机开环速度控制

11

2 | 双电机开环位置控制
3 | AS5600 双编码器测试
4 | 双电机闭环速度控制
5 | 一个电机作为旋钮，另外一个电机输出速度
6 | 双电机闭环位置/力矩互控
7 | 灯哥开源机器狗专用程序（通过串口控制此 FOC 驱动板）
8 | 灯哥开源机器狗专用程序（通过串口控制此 FOC 驱动板）
9 | 双电机力矩控制
10 | SimpleFOC Studio 快速调节 PID-驱动板端例程

例程运行标准效果视频：

效果运行视频 (https://www.bilibili.com/video/BV1QU4y1p7Z6/)

测试自己板子时可以根据此视频查看自己的板子是否达到标准效果。

## 6 从0开始焊接电路板（针对自行DIY此FOC

## 驱动的爱好者）

手把手焊接教学 (https://www.bilibili.com/video/BV1QU4y1p7Z6?p=2)

## 7 常见问题及其解决

### 7.1 电机不转

1. 检查电机的接线是否正常
2. 检查电源是否没电

12

3. 检查程序是否正确
4. 检查电机内部是否断线

### 7.2 电机抖动

1. 检查电机接线，是否存在缺相
2. 检查程序中的极对数设置是否正确（一般震动现象大部分来源于

极对数设置错误）

3. 测试开环速度例程，如果由于速度设置过高引起震动，可以把速

度设置低些

### 7.3 电机或芯片剧烈发热

1. 电机不要运动在震动状态下
2. 开环速度例程，速度不要长期设置为 0（否则类似堵转，会发热），

若要取得实用效果，建议闭环

3. 开环位置例程，位置不要长期不变（否则类似堵转，会发热），

若要取得实用效果，建议闭环

### 7.4 编码器读数跳变

1. 检查编码器磁铁安装是否正确（轴向，径向磁铁要分清）
2. AS5600 的话，检查是否 dir 接入高电平或者低电平（GND）
3. 检查磁铁和编码器得距离是否过远

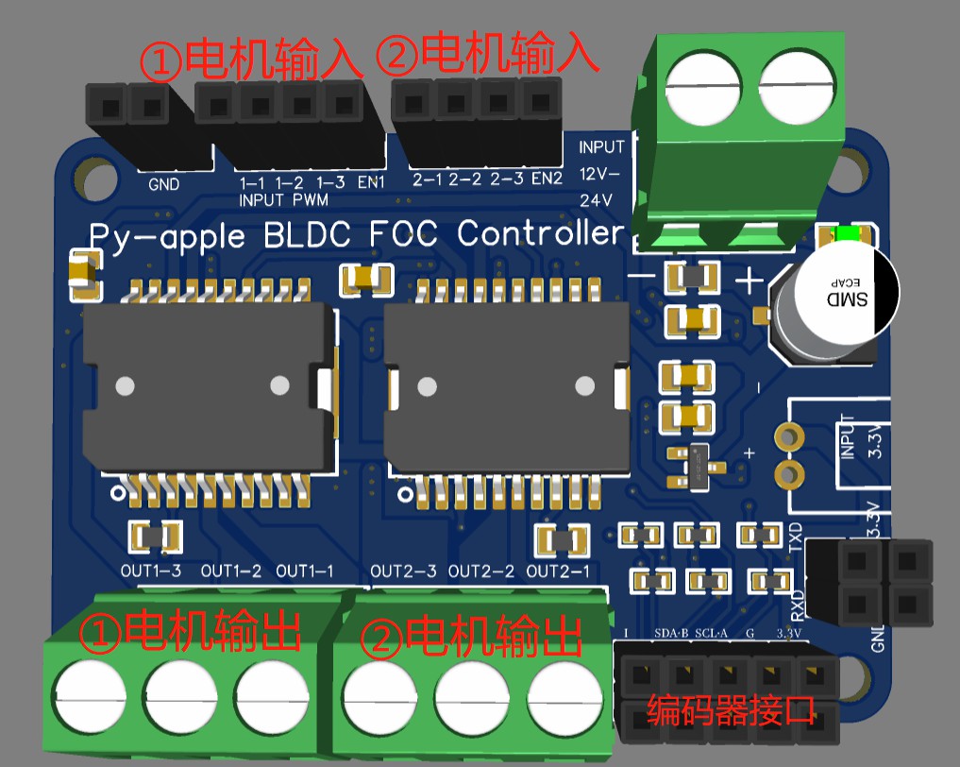
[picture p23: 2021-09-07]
pic/pafoc_interface.jpg

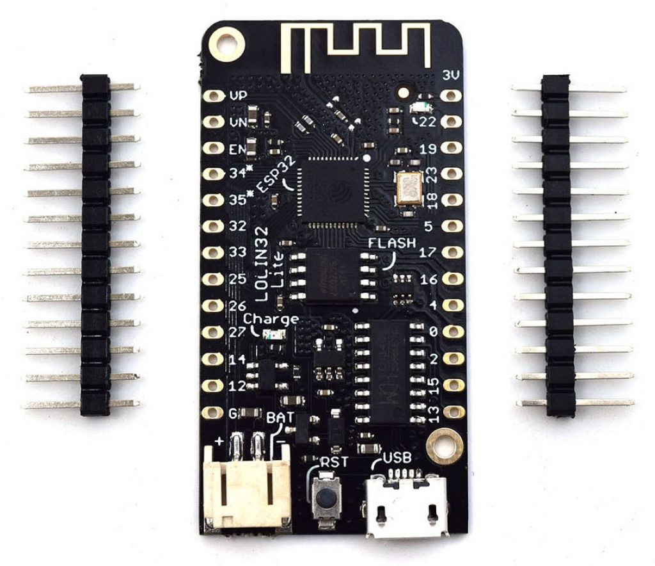
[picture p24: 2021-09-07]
pic/lolin32_lite.jpg

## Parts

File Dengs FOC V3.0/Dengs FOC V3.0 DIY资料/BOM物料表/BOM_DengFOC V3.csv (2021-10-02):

ID | Name | Designator | Footprint | Quantity | Manufacturer Part | Manufacturer | Supplier | Supplier Part | Price
1 | 47uF | C1,C2 | C0603 | 2 | GRM188R60J476ME15D | MuRata | LCSC | C140782 | 0.6055
2 | 4.7uF | C3,C8 | C0805 | 2 | CL21A475KBQNNNE | SAMSUNG | LCSC | C98192 | 0.2296
3 | 100nF | C4,C18 | C0805__ | 2 | C0805X104K101T | HEC(Holy Stone Enterprise) | LCSC | C485772 | 0.0992
4 | 100uF | C5,C19 | CAP-SMD_BD6.3-L6.6-W6.6-FD | 2 | RVE1V101M0607 | ROQANG | LCSC | C99837 | 0.3797
5 | 220nF | C6,C20 | C0805__ | 2 | CL21B224KBFNNNE | SAMSUNG | LCSC | C5378 | 0.0781
6 | 1uF | C7,C22 | C0805__ | 2 | CL21B105KBFNNNE | SAMSUNG | LCSC | C28323 | 0.06
7 | 100nF | C10,C17,C24,C26 | C0603 | 4 | CC0603KRX7R9BB104 | YAGEO | LCSC | C14663 | 0.0164
8 | 10nF | C11,C25 | C0805__ | 2 | CL21A106KAYNNNE | SAMSUNG | LCSC | C15850 | 0.0725
9 | 8.2nF | C12 | C0603 | 1 | CL10B822KB8NNNC | SAMSUNG | LCSC | C27920 | 0.1011
10 | 1.2nF | C14 | C0603 | 1 | FN18X122K500PSG | PSA(Prosperity Dielectrics) | LCSC | C565591 | 0.0483
11 | 10pF | C15 | C0603 | 1 | CC0603JRNPO9BN100 | YAGEO | LCSC | C106245 | 0.0198
12 | 22uF | C27,C28 | C0603 | 2 | CL10A226MQ8NRNC | SAMSUNG | LCSC | C59461 | 0.0659
13 | LBAT54SLT1G | D1,D3 | SOT-23_L2.9-W1.3-P1.90-LS2.4-BR | 2 | LBAT54SLT1G | LRC | LCSC | C12765 | 0.0684
14 | SS36 | D2 | SMA_L4.3-W2.6-LS5.2-RD | 1 | SS36 | MDD | LCSC | C16015 | 0.3541
15 | SS34F_C908239 | D5 | SMAF_L3.5-W2.6-LS4.7-FD | 1 | SS34F | FUXINSEMI | LCSC | C908239 | 0.3438
16 | Header-Female-2.54_2x9 | H1 | HDR-TH_18P-P2.54-V-R2-C9-S2.54 | 1 | Header-Female-2.54_2x9 | BOOMELE | LCSC | C71956 | 0.7998
17 | 6.8uH | L1 | IND-SMD_L5.0-W5.0_SWPA5040S | 1 | SWPA5040S6R8M | Sunlord | LCSC | C36411 | 0.3861
18 | 17-21SUYC/TR8 | LED1 | LED0805-RD | 1 | 17-21SUYC/TR8 | KENTO | LCSC | C2296 | 0.0741
19 | WJ126V-5.0-3P | P1,P2 | CONN-TH_3P-P5.00_WJ126V-5.0-3P | 2 | WJ126V-5.0-3P | ReliaPro | LCSC | C8401 | 0.5956
20 | WJ126V-5.0-2P | P3 | CONN-TH_WJ126V-5.0-2P | 1 | WJ126V-5.0-2P | ReliaPro | LCSC | C8404 | 0.3967
21 | 0 | R2 | R0805 | 1 | RM10FTN0 | TA-I Tech | LCSC | C254574 | 0.0092
22 | 1K | R3 | R0805 | 1 | 0805W8F1001T5E | UniOhm | LCSC | C17513 | 0.0132
23 | 330K | R4 | R0603 | 1 | 0603WAF3303T5E | UniOhm | LCSC | C23137 | 0.0067
24 | 68K | R5 | R0603 | 1 | 0603WAF6802T5E | UniOhm | LCSC | C23231 | 0.0067
25 | 30K | R6 | R0603 | 1 | 0603WAF3002T5E | UniOhm | LCSC | C22984 | 0.0069
26 | 10K | R9 | R0603 | 1 | 0603WAF1002T5E | UniOhm | LCSC | C25804 | 0.0066
27 | 1.87K | R10 | R0603 | 1 | 0603WAF1871T5E | UniOhm | LCSC | C22850 | 0.0079
28 | 0.01 | R15,R16,R17,R18 | R1206 | 4 | RTT06R010FTP | RALEC | LCSC | C104920 | 0.0836
29 | 4.7K | RN1,RN2 | RES-ARRAY-SMD_0603-8P-L3.2-W1.6-BL | 2 | 4D03WGF4701T5E | UniOhm | LCSC | C66697 | 0.0629
30 | L6234PD013TR | U1,U4 | POWERSO20_L15.9-W11.0-P1.27-LS14.2-BL-EP | 2 | L6234PD013TR | STMicroelectronics | LCSC | C77581 | 31.28
31 | micropython esp32 | U2 | MICROPYTHON ESP32 | 1
32 | TPS54331DDAR | U3 | SOIC-8_L5.0-W4.0-P1.27-LS6.0-BL-EP | 1 | TPS54331DDAR | TI | LCSC | C90761 | 9.5
33 | INA240A2PWR | U6,U7,U8,U9 | TSSOP-8_L4.4-W3.0-P0.65-LS6.4-BL | 4 | INA240A2PWR | TI | LCSC | C129949 | 13.75
34 | AMS1117-3.3 | U10 | SOT-223-3_L6.5-W3.4-P2.30-LS7.0-BR | 1 | AMS1117-3.3 | AMS | LCSC | C6186 | 1.0381

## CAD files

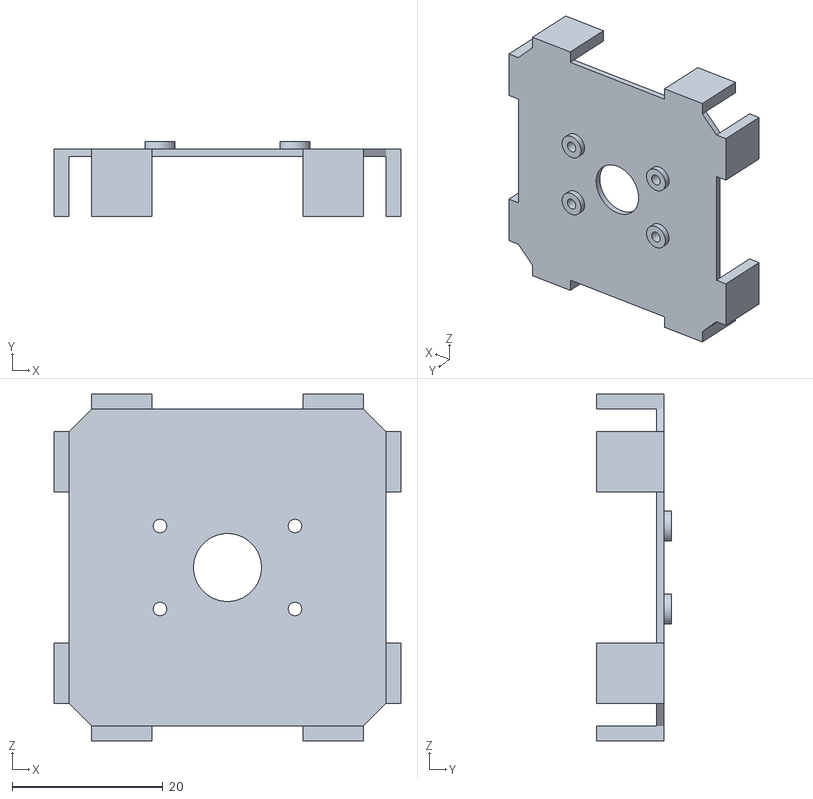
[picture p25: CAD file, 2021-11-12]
Dengs FOC V3.0/Dengs FOC V3.0 测试例程(支持库SimpleFOC 2.2.1)/AS5047P编码器安装在42步进电机背面的架子-3D打印.stl
46.0 x 10.0 x 46.0

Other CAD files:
Dengs FOC V3.0/Dengs FOC V3.0 测试例程(支持库SimpleFOC 2.2.1)/AS5600编码器安装在42步进电机背面的架子-3D打印.stl

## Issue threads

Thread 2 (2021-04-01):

你文档里对应的那个电机，规格跟购买链接发一下

wei1224hf, 2021-04-01:
你文档里对应的那个电机，规格跟购买链接发一下
不然自己去找10欧姆相阻，功率120瓦左右的云台电机，好麻烦
我手上只有一个DJ6010电机，估计是不符合要去的

还有你文档上， 电机接线，三根相线能否标注一下 ABC 或 UVW 或者 红黑蓝？

huhu415, 2021-11-14:
电机只要是云台电机就行，电机接线不分abc

mzhboy, 2021-12-15:
目测是stm32 foc开发套件里面的电机，单买很贵的

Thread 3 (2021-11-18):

25.40毫米的针脚？

samuk, 2021-11-18:
你好，我很高兴找到你的项目，看起来很适合制作小型机器人!

我对使用你的2.0板做一个开放的硬件机器人感兴趣。我打算使用ESP32-DevKit-Lipo-EA，来自https://www.olimex.com/Products/IoT/ESP32/ESP32-DevKit-LiPo/open-source-hardware
引脚是25.40mm https://dl.espressif.com/dl/DXF_ESP32-S3-DevKitC-1_V1_20210312CB.pdf

这是否与你们的2.0板兼容？还是新的3.0？

谢谢。

珊珊

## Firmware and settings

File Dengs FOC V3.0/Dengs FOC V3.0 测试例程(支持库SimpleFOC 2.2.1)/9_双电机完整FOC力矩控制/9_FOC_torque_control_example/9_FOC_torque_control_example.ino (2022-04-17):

/**
Deng's FOC 双电机 FOC电流控制例程 测试库：SimpleFOC 2.2.1 测试硬件：灯哥开源FOC V3.0
在串口窗口中输入：A+电流控制M0，B+电流控制M1，电流单位为A
setup()中可取消注释设置电压限制与电流限制
在使用自己的电机时，请一定记得修改默认极对数，即 BLDCMotor(14) 中的值，设置为自己的极对数数字
程序默认设置的供电电压为 16.8V,用其他电压供电请记得修改 voltage_power_supply , voltage_limit 变量中的值
默认PID针对的电机是 GB6010 ，使用自己的电机需要修改PID参数，才能实现更好效果
*/

#include <SimpleFOC.h>

//电机实例
BLDCMotor motor1 = BLDCMotor(14);
BLDCDriver3PWM driver1 = BLDCDriver3PWM(32,33,25,22);

BLDCMotor motor2 = BLDCMotor(14);
BLDCDriver3PWM driver2  = BLDCDriver3PWM(26,27,14,12);

//编码器实例
MagneticSensorI2C sensor1 = MagneticSensorI2C(AS5600_I2C);
TwoWire I2Cone = TwoWire(0);
MagneticSensorI2C sensor2 = MagneticSensorI2C(AS5600_I2C);
TwoWire I2Ctwo = TwoWire(1);


// 在线电流检测实例
InlineCurrentSense current_sense1 = InlineCurrentSense(0.01, 50.0, 39, 36);
InlineCurrentSense current_sense2 = InlineCurrentSense(0.01, 50.0, 35, 34);

// commander通信实例
Commander command = Commander(Serial);
void doMotor1(char* cmd){ command.motor(&motor1, cmd); }
void doMotor2(char* cmd){ command.motor(&motor2, cmd); }

void setup() {
  // 编码器设置
  I2Cone.begin(19,18, 400000UL); 
  I2Ctwo.begin(23,5,400000UL); 
  sensor1.init(&I2Cone);
  sensor2.init(&I2Ctwo);
  motor1.linkSensor(&sensor1);
  motor2.linkSensor(&sensor2);
  

  // 驱动器设置
  driver1.voltage_power_supply = 16.8;
  driver1.init();
  motor1.linkDriver(&driver1);
  driver2.voltage_power_supply = 16.8;
  driver2.init();
  motor2.linkDriver(&driver2);

  // 电流限制
//    motor1.current_limit = 2;
//    motor2.current_limit = 2;
    // 电压限制
//    motor1.voltage_limit = 12;
//    motor2.voltage_limit = 12;


  // 电流检测
  current_sense1.init();
  current_sense1.gain_b *= -1;
  current_sense1.skip_align = true;
  motor1.linkCurrentSense(&current_sense1);
  // current sense init and linking
  current_sense2.init();
  current_sense2.gain_b *= -1;
  current_sense2.skip_align = true;
  motor2.linkCurrentSense(&current_sense2);

  // 控制环
  // 其他模式 TorqueControlType::voltage TorqueControlType::dc_current 
  motor1.torque_controller = TorqueControlType::foc_current; 
  motor1.controller = MotionControlType::torque;
  motor2.torque_controller = TorqueControlType::foc_current; 
  motor2.controller = MotionControlType::torque;

  // FOC电流控制PID参数
   motor1.PID_current_q.P = 5;
   motor1.PID_current_q.I= 1000;
   motor1.PID_current_d.P= 5;
   motor1.PID_current_d.I = 1000;
   motor1.LPF_current_q.Tf = 0.002; // 1ms default
   motor1.LPF_current_d.Tf = 0.002; // 1ms default

   motor2.PID_current_q.P = 5;
   motor2.PID_current_q.I= 1000;
   motor2.PID_current_d.P= 5;
   motor2.PID_current_d.I = 1000;
   motor2.LPF_current_q.Tf = 0.002; // 1ms default
   motor2.LPF_current_d.Tf = 0.002; // 1ms default

    // 速度环PID参数
    motor1.PID_velocity.P = 0.05;
    motor1.PID_velocity.I = 1;
    motor1.PID_velocity.D = 0;

    motor2.PID_velocity.P = 0.05;
    motor2.PID_velocity.I = 1;
    motor2.PID_velocity.D = 0;
    // default voltage_power_supply
  
    // 速度限制
    motor1.velocity_limit = 20;
    motor2.velocity_limit = 20;


  // monitor接口设置
  Serial.begin(115200);
  // comment out if not needed
  motor1.useMonitoring(Serial);
  motor2.useMonitoring(Serial);

  // monitor相关设置
  motor1.monitor_downsample = 0;
  motor1.monitor_variables = _MON_TARGET | _MON_VEL | _MON_ANGLE;
  motor2.monitor_downsample = 0;
  motor2.monitor_variables = _MON_TARGET | _MON_VEL | _MON_ANGLE;
  


  //电机初始化
  motor1.init();
  // align encoder and start FOC
  motor1.initFOC(); 
  
  motor2.init();
  // align encoder and start FOC
  motor2.initFOC(); 

  // 初始目标值
  motor1.target = 0.05;
  motor2.target = 0.05;

  // 映射电机到commander
  command.add('A', doMotor1, "motor 1");
  command.add('B', doMotor2, "motor 2");

  Serial.println(F("Double motor sketch ready."));
  
  _delay(1000);
}


void loop() {
  // iterative setting FOC phase voltage
  motor1.loopFOC();
  motor2.loopFOC();

  // iterative function setting the outter loop target
  motor1.move();
  motor2.move();

  // user communication
  command.run();
  motor1.monitor();
  motor2.monitor();
}

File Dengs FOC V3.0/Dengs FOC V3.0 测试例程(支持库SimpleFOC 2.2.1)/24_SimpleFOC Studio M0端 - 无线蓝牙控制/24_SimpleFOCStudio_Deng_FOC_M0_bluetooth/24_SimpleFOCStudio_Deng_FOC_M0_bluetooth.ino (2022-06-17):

/**
Deng's FOC M0 FOC电流控制例程 适用于SimpleFOC Studio 测试库：SimpleFOC 2.2.1 测试硬件：灯哥开源FOC V3.0
在串口窗口中输入：M+电流，就可以使得M0电机闭环转动，电流单位为A
setup()中可取消注释设置电压限制与电流限制
在使用自己的电机时，请一定记得修改默认极对数，即 BLDCMotor(14) 中的值，设置为自己的极对数数字
程序默认设置的供电电压为 16.8V,用其他电压供电请记得修改 voltage_power_supply , voltage_limit 变量中的值
默认PID针对的电机是 GB6010 ，使用自己的电机需要修改PID参数，才能实现更好效果
*/

#include <SimpleFOC.h>
#include "BluetoothSerial.h"

#if !defined(CONFIG_BT_ENABLED) || !defined(CONFIG_BLUEDROID_ENABLED)
#error Bluetooth is not enabled! Please run `make menuconfig` to and enable it
#endif

BluetoothSerial SerialBT;
// BLDC motor & driver instance
BLDCMotor motor = BLDCMotor(14);
BLDCDriver3PWM driver = BLDCDriver3PWM(32,33,25,22);

// encoder instance
MagneticSensorI2C sensor = MagneticSensorI2C(AS5600_I2C);
TwoWire I2Cone = TwoWire(0);


// inline current sensor instance
// check if your board has R010 (0.01 ohm resistor) or R006 (0.006 mOhm resistor)
InlineCurrentSense current_sense = InlineCurrentSense(0.01, 50.0, 39, 36);

// commander communication instance
Commander command = Commander(SerialBT);
void doMotor(char* cmd){ command.motor(&motor, cmd); }

void setup() {
  I2Cone.begin(19,18, 400000UL); 
  sensor.init(&I2Cone);
  motor.linkSensor(&sensor);
  // driver config
  // power supply voltage [V]
  //driver.pwm_frequency = 100000;
  driver.voltage_power_supply = 16.8;
  driver.init();
  // link driver
  motor.linkDriver(&driver);

    // 电流限制
//    motor.current_limit = 2;
    // 电压限制
//    motor.voltage_limit = 12;

  // TorqueControlType::foc_current
  // 其他模式 TorqueControlType::voltage TorqueControlType::dc_current 
  motor.torque_controller = TorqueControlType::foc_current; 
  // set control loop type to be used
  motor.controller = MotionControlType::torque;

  // contoller configuration based on the controll type 
  motor.PID_velocity.P = 0.2;
  motor.PID_velocity.I = 10;
  motor.PID_velocity.D = 0;
  // default voltage_power_supply
  motor.voltage_limit = 12;
  
  // velocity low pass filtering time constant
  motor.LPF_velocity.Tf = 0.01;

  // angle loop controller
  motor.P_angle.P = 20;
  // angle loop velocity limit
  motor.velocity_limit = 20;

  // use monitoring with serial for motor init
  // monitoring port
  //Serial.begin(115200);
  SerialBT.begin("DengFOC"); //Bluetooth device name
  // comment out if not needed
  motor.useMonitoring(SerialBT);
  motor.monitor_downsample = 0; // disable intially
  motor.monitor_variables = _MON_TARGET | _MON_VEL | _MON_ANGLE; // monitor target velocity and angle
  
  // current sense init and linking
  current_sense.init();
  current_sense.gain_b *= -1;
  motor.linkCurrentSense(&current_sense);

  // initialise motor
  motor.init();
  // align encoder and start FOC
  motor.initFOC(); 

  // set the inital target value
  motor.target = 0.05;

  // subscribe motor to the commander
  command.add('M', doMotor, "motor");

  // Run user commands to configure and the motor (find the full command list in docs.simplefoc.com)  
  SerialBT.println(F("Motor commands sketch | Initial motion control > torque/voltage : target 2V."));
  
  _delay(1000);
}


void loop() {
  //SerialBT.println(F("111"));
  // iterative setting FOC phase voltage
  motor.loopFOC();

  // iterative function setting the outter loop target
  motor.move();

  // motor monitoring
  motor.monitor();

  // user communication
  command.run();
}

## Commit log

2021-09-07 upload Arduino IDE
2021-09-24 update v2 bom
    [BOM.csv, BOM_DengFOC v2.0.1 release.csv]
2021-09-24 update bom
    [BOM.csv, BOM_DengFOC v2.0.1 release.csv]
2021-10-02 Deng FOC V3 update
    [BOM_DengFOC V3.csv]
2021-10-27 fix errors
    fix link in docs
    fix as5600 test
    [3_dual_as5600_test.ino]
2021-11-07 update stepper example
    [as5600_42_Steppertest_gap.stl]
2021-11-12 update AS5047P example
    [42_as5047p_test_gap.stl]
2021-11-12 update as5047p example to v2
    [42_as5047p_test_gap.stl]
2021-11-13 update encoder stl
    [AS5047P编码器安装底座.stl, AS5600编码器安装底座.stl]
2021-12-08 update v3 sch pcb
2021-12-31 Revert "Merge branch 'master' of https://github.com/ToanTech/Deng-s-foc-controller"
    This reverts commit 441e8f4eb0bc22794474044e604fc1f4b06ba2d3, reversing
    changes made to 8691d0725c9aa75b315d25515e2bc0c47b019db3.
    [42_as5047p_test_gap.stl, AS5047P编码器安装底座.stl, AS5600编码器安装底座.stl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]
2022-03-27 update hall examples
    update hall examples
    hall sensor test
    hall motor test
2022-04-11 update stl
    [AS5047P编码器安装在42步进电机背面的架子-3D打印.stl, AS5600编码器安装在42步进电机背面的架子-3D打印.stl]
2022-04-16 update new arduino
    [AS5047P编码器安装在42步进电机背面的架子-3D打印.stl, AS5600编码器安装在42步进电机背面的架子-3D打印.stl]
2022-04-23 Update 灯哥开源FOC V3.0使用文档V5(2022423).pdf
